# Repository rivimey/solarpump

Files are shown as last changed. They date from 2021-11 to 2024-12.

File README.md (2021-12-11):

Solar powered Water pump controller
===================================

## Introduction

The project has been to put together a water pump powered by a solar panel, with a battery
for reserve power. The need was to pump water from a stream beside allotment garden up to
the allotment for watering plants. The whole unit needs to be completely portable because
the area was was prone to theft.

## Initial version

An initial version was created using off the shelf components, and it worked to a degree.
The solar panel linked to the battery using a cheap solar controller, PWM based, and the
rest of the circuit was wire and switches.

Parts:

 - VerRich Diaphragm pump, 12V Water Pumps 70W Self Priming Pump 6 L/Min

 - Photonic Universe 10A Solar Charge Controller for up to 160W panel.

 - BETOP 60W foldable solar panel kit, 18V.

 - 12V LED Panel Digital Voltmeter Color LED Digital Display
 
 - 12V 20A illuminated rocker switches.

 - 3-pin XLR plugs and sockets for the Solar input

This was constructed with the battery, controller and other wiring inside a wooden box
bought from Amazon, and with the pump screwed to the top (this helps ensure that any
drips of water and electricity don't interact!)

## Second design

A second version was designed with the intention of supporting MPPT conversion and also
to provide additional information about the current flows. This was because placement of
the panel in the prevailing sunlight was easier when you have feedback on what is going
on.

However, this second design was never built -- I was never sure enough it would work to
make it worth getting a PCB built. I had done a lot of reading around the topic of MPPT
converters and was starting to get some idea of the issues and constraints, and could
see that what I had would probably have issues.

I did get as far as a KiCad PCB design, though:

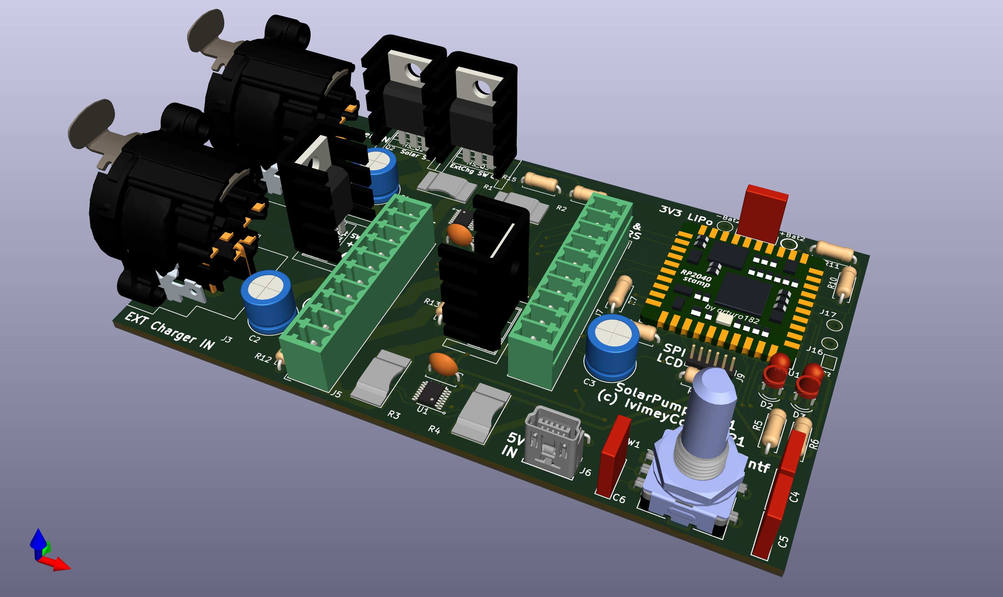
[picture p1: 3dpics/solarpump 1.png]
The abandoned Solarpump v2


## Second build

A new version was built... mostly using the components of the first version in a larger
box (a two bottle "wine presentation" box with a nice looking, and water repellant, red
varnish). This allowed a much better arrangement of the wiring, and made room for a 12V
Car Accessory connector, which was supposed to be helpful for a camping trip.

For this version, a 3D CAD model was built in Blender 3D to verify the dimensions and
fit.

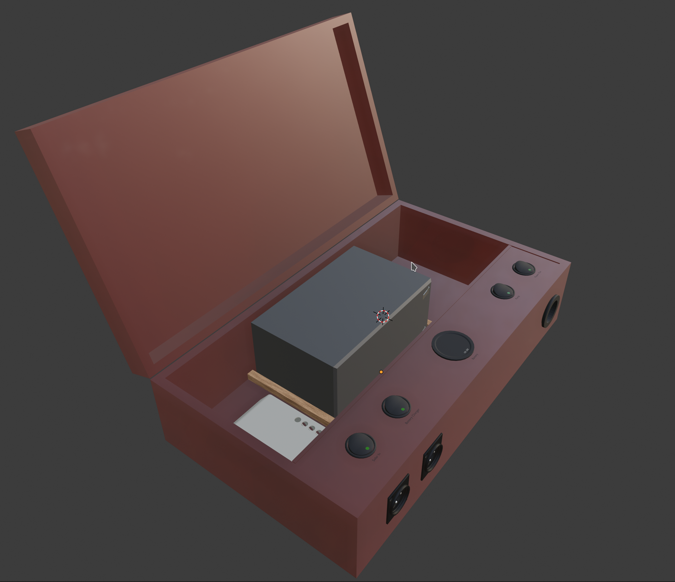
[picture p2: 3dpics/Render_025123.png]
Solar pump in its new box


## Third design

An Intervention came along, in the way of the "DIY 1KW MPPT Solar Charge Converter"
build, published on Instructables. This finally showed a path -- to be fair, not
so very different from my earlier attempt but far better explained and, critically,
tested! I resolved to rebuild my earlier design around this base.

The Instructables build is https://www.instructables.com/DIY-1kW-MPPT-Solar-Charge-Controller/
and there are links to the firmware and design files in that article.

A design goal for this version was to increase the flow rate somewhat, as although the
existing pump worked, it was rather slow. I eventually settled on the Seaflo 41 Series
DC Water System Pump 12V 12.5 LPM, which is up to about 2.5x higher flow rate.

Another design goal is to support measurement of water flow rate, so the unit can
keep track of total water pumped and water pumped per session. While not strictly
necessary this was something I felt was important.

Compared to that version, I decided to:

  - use the Solderparty RP2040 Stamp, partly because I had it and like it;

  - use an alternate half-bridge driver, because the 2104/5 is out of stock at present
    and the new one integrates a diode;

  - use an alternate current sensor (ACS758), because the article was quite critical of
    the one suggested (ACS712). I can't tell from the datasheet if it's an improvement,
    though :-(

  - use more current sensors, to avoid needing to estimate current output from current
    input, partly to monitor more things directly;

  - use 3 separate SM power supply devices for local power, rather than the arrangement
    in the original, which looked clunky;

  - use a different, and 8 channel, ADC to measure the extra circuits, and also enabling
    fast 16-bit sampling and faster MCU comms via SPI. It's slightly more expensive but
    not a lot, and overall better;

The big change I added was one I alluded to in an earlier mail: I essentially have 2
separate buck converters now, rather than just one, because I wanted to:

  - support MPPT input (eg. 18V);

  - support a controllable battery voltage for charging/float purposes (eg. 15V);

  - support a controllable output voltage (sep from battery) to e.g. control DC pump
    speed (eg. 9V to 12.5V).

So I've essentially got:  MPPT => [Battery] => Simple Buck => Output.

This circuit then has two, switchable, outputs, rather than one, which I hope I've
designed right this time! The purpose is to support a fixed link to the pump, plus an
'Aux' circuit for e.g. a car cig socket, for use when e.g. camping. My intention is that
the two outputs are not used at the same time, but the circuit allows that option. I
decided that USB power delivery, while nice, would be via a commercial car adapter,
not built in.

I have derated the components slightly compared to the original, supporting only up
to 48V input and up to about current output 18A rather than the 80V and 30A original,
as this is meant to be a portable unit and not destined for huge batteries or panel
arrays. On the battery front I'm intending to change from a 12V lead acid battery to
a 4S3P Lithium one based on twelve 18650 batteries + controller for a 14V output. It
should help reduce the weight (the new pump, now 3 gal/min rather than 1gal/min of
earlier, is heavier!).

The second smaller board is for a 'front panel', which I envisage with a large
"emergency stop" pushbutton, a digital rotary encoder, and a Pimoroni "Pico Display
Hat", which is a small LCD on a 40pin R-Pi Pico footprint with 4 small pushbuttons and
an RGB led. Most of that is interfaced via an MCP 16-pin IO adapter on the I2C bus,
except for the SPI bus for the display itself.

Not shown in the circuit because it's off-board, the main on/off switch will be an
SPST switch between the battery and the PCB.

Some pictures of the build so far (from KiCad):

PCB for Solarpump v3

PCB for Solarpump v3

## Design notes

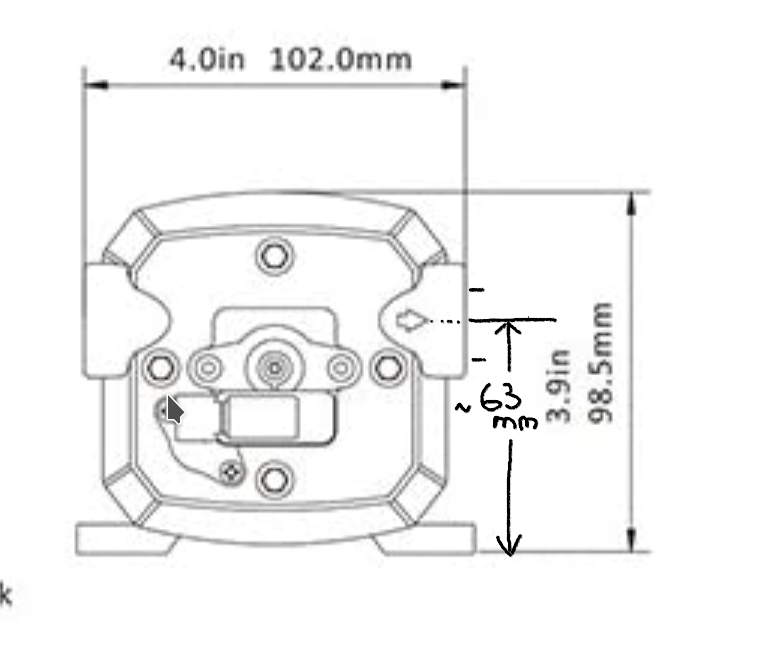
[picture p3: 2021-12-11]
Docs/Pump_outline.png

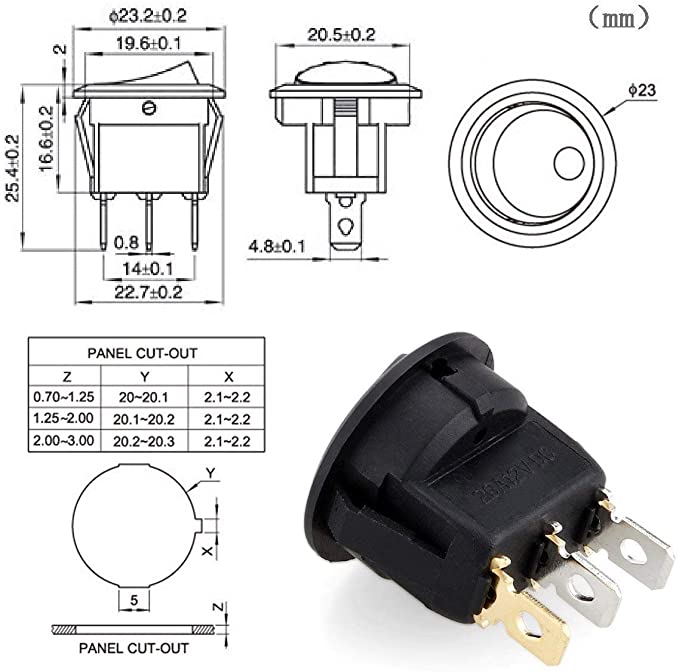
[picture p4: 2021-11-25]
Docs/Toggle_SW_618fWi4n+FL.AC_SX679.jpg

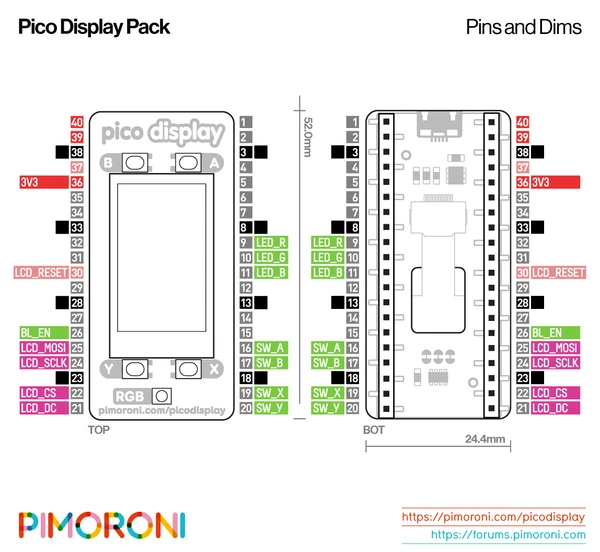
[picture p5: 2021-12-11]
Docs/displaypack_600x600.png

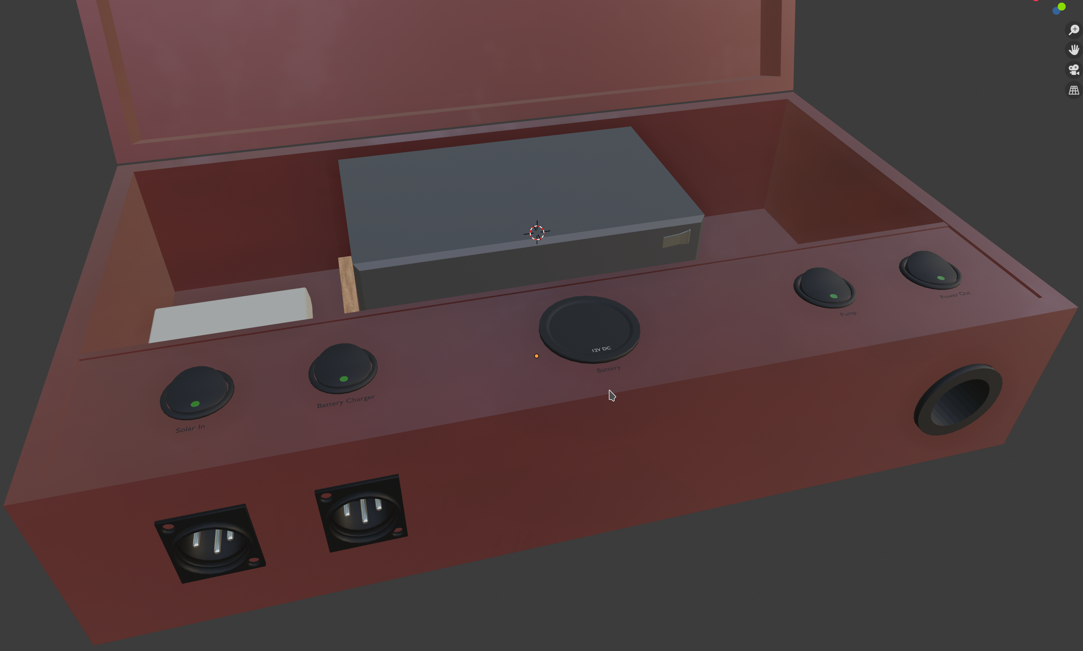
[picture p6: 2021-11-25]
3dpics/Render_025204.png

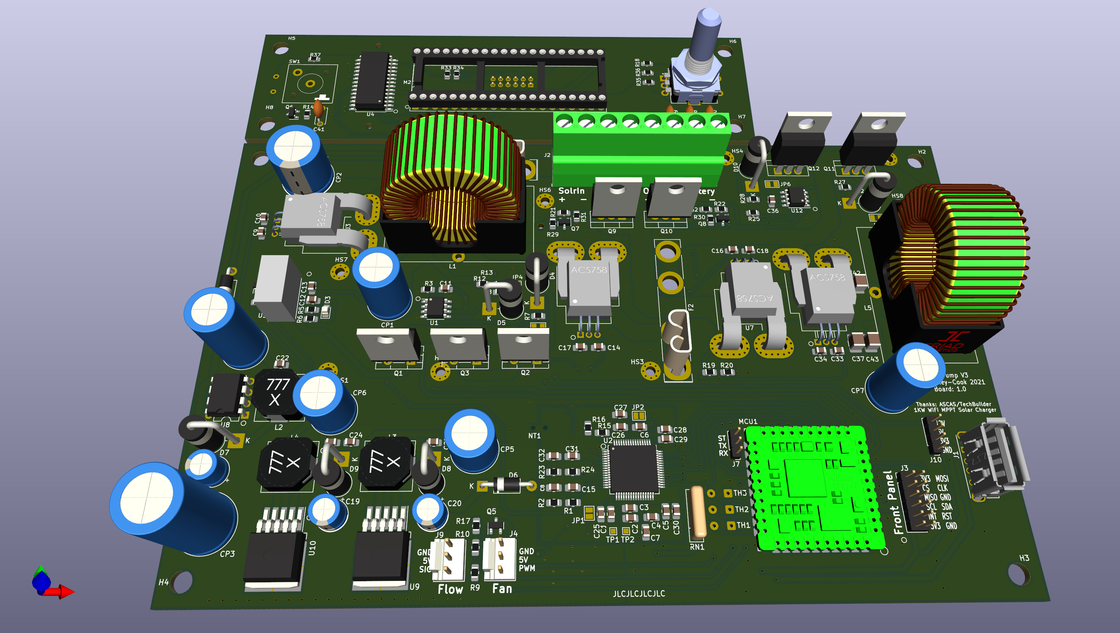
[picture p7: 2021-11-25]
3dpics/solarpumpv3_2.png

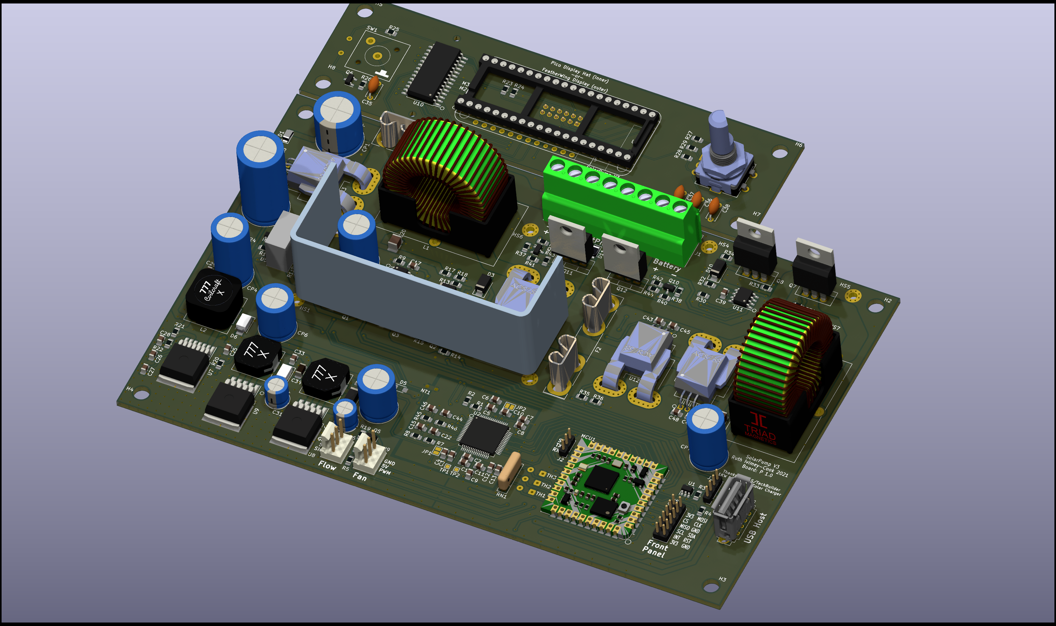
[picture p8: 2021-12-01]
3dpics/solarpump3_11r.png

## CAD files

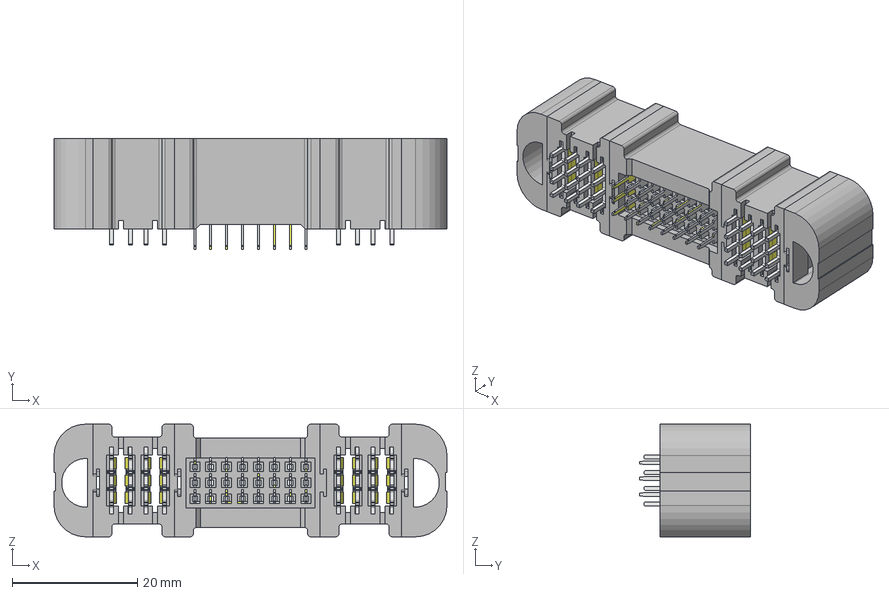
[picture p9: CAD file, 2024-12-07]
3dmodels/ET60S-D02-3-08-D02-X-V1-S.step
62.8 x 17.7 x 18.0 mm
ET60S-24-V1_signal_terminal
ET60S-D02-V1_power_terminal x 2
ET60S-V1_guide_post_left
ET60S-D02-V1_power_pins x 2
ET60S-D02-V12_power_pins x 2
ET60S-V1_guide_post_right
ET60S-24-V1_signal_pins
ET60S-24-V12_signal_pins

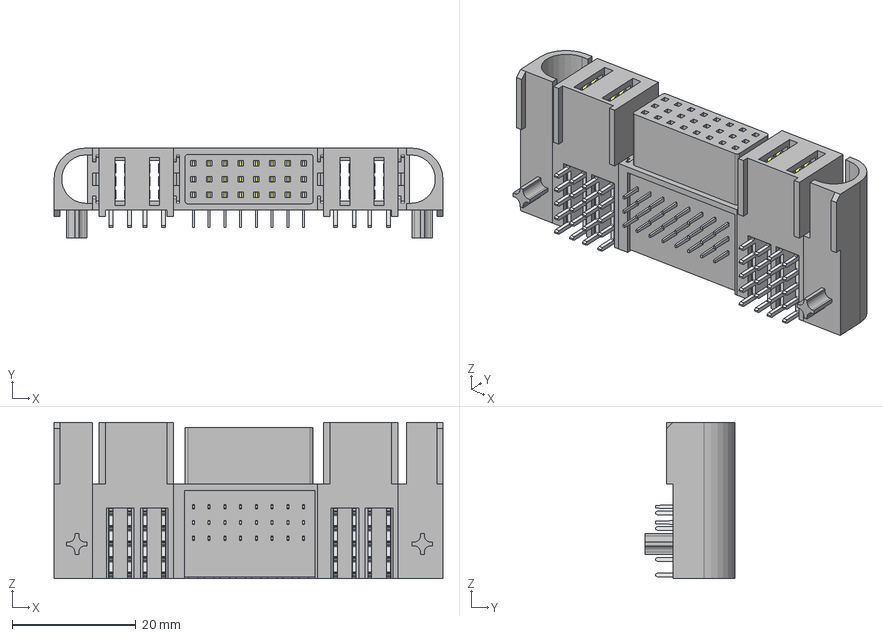
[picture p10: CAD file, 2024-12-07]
3dmodels/ET60S-D02-3-08-D02-L-R1-S.stp
62.8 x 14.5 x 25.2 mm
ET60S-24-R1_signal_terminal
ET60S-D02-R1_power_terminal x 2
ET60S-R1_guide_post_left
ET60S-D02-R1_power_pins x 2
ET60S-D02-R12_power_pins x 2
ET60S-R1_guide_post_right
ET60S-24-R1_signal_pins
ET60S-24-R12_signal_pins

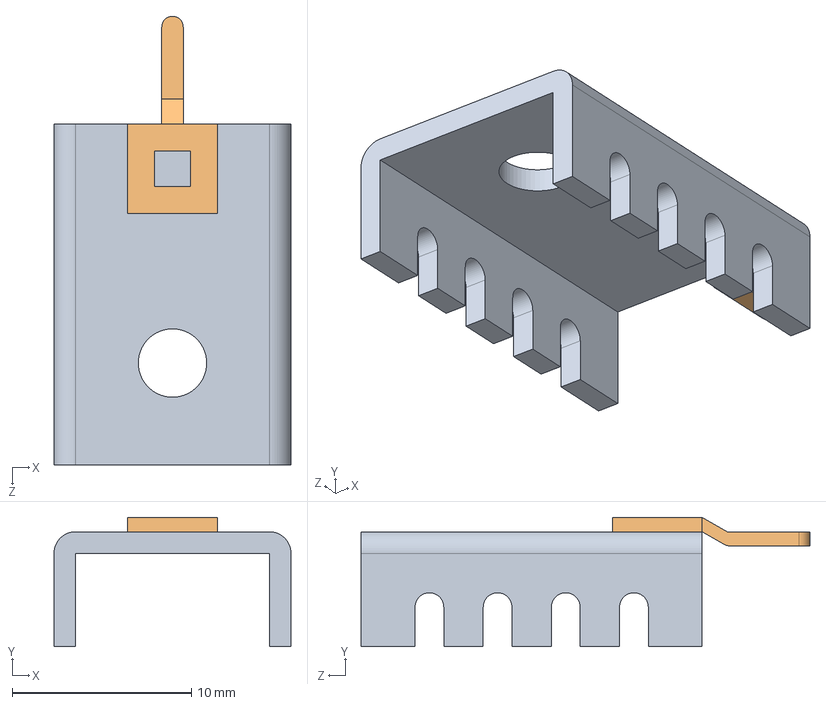
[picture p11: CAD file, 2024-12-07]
3dmodels/User Library-D01PA.STEP
13.2 x 7.20 x 25.0 mm

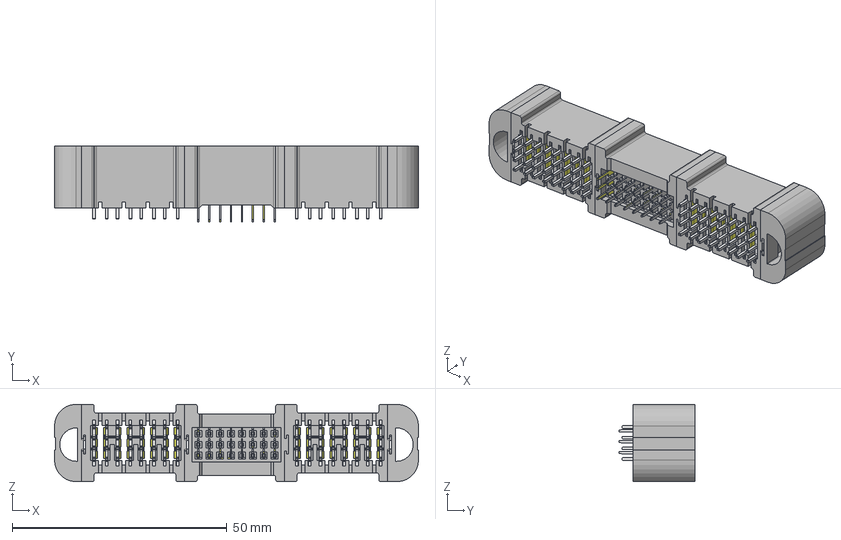
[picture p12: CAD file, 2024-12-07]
3dmodels/ET60S-D04-3-08-D04-X-V1-S.step
84.8 x 17.7 x 18.0 mm
ET60S-24-V1_signal_terminal
ET60S-D04-V1_power_terminal x 2
ET60S-V1_guide_post_left
ET60S-D04-V1_power_pins x 2
ET60S-D04-V12_power_pins x 2
ET60S-V1_guide_post_right
ET60S-24-V1_signal_pins
ET60S-24-V12_signal_pins

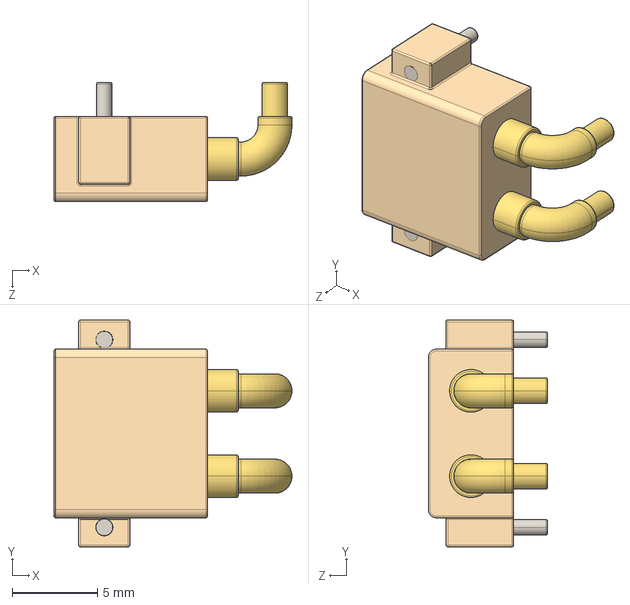
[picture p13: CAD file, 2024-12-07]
3dmodels/AMASS-XT30PW-M.STEP
13.9 x 13.3 x 7.00 mm

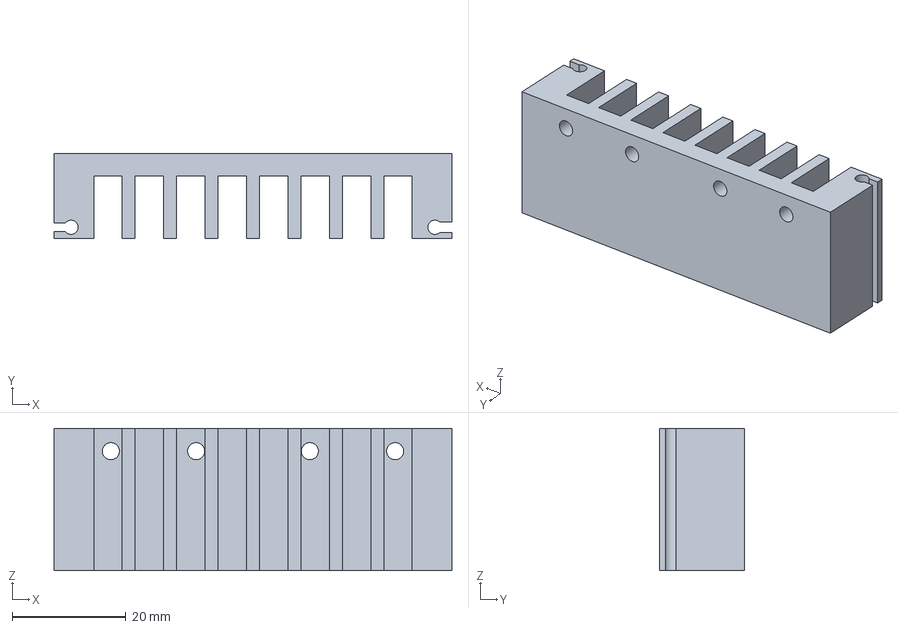
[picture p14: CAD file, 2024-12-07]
3dmodels/RADIATEUR_4_TROUS.step
70.0 x 15.0 x 25.0 mm

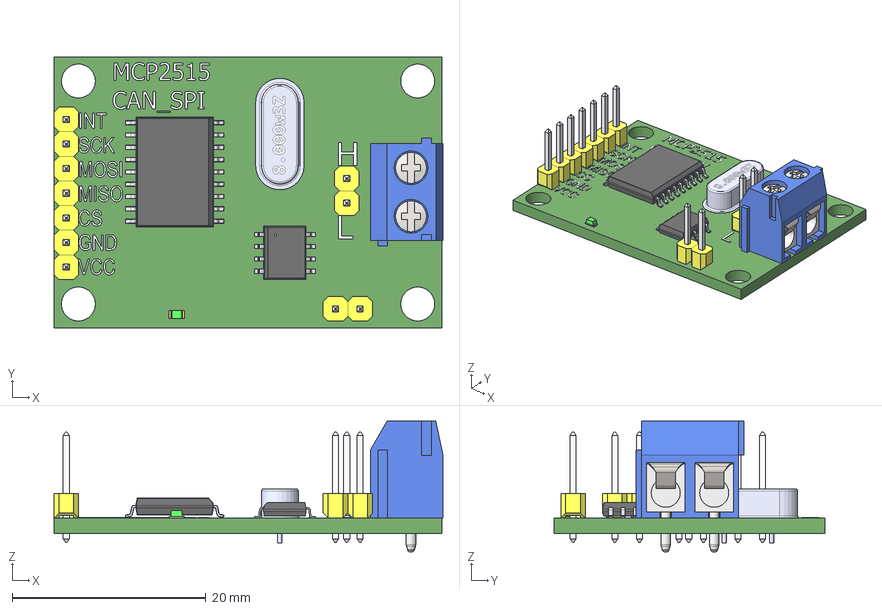
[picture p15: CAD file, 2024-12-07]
3dmodels/MCP2515 CAN_SPI.step
40.1 x 28.0 x 13.5 mm
so_ic_wide_18pin
PCB CAN SPI
so_ic_8pin
led_green_0603
ABRACON_ABL-8.000MHZ-B2
Pin Header 7 x 1 TH 2.54mm Pitch
Pin Header 2 x1 TH 2.54mm Pitch x 2
TE_1776244-2

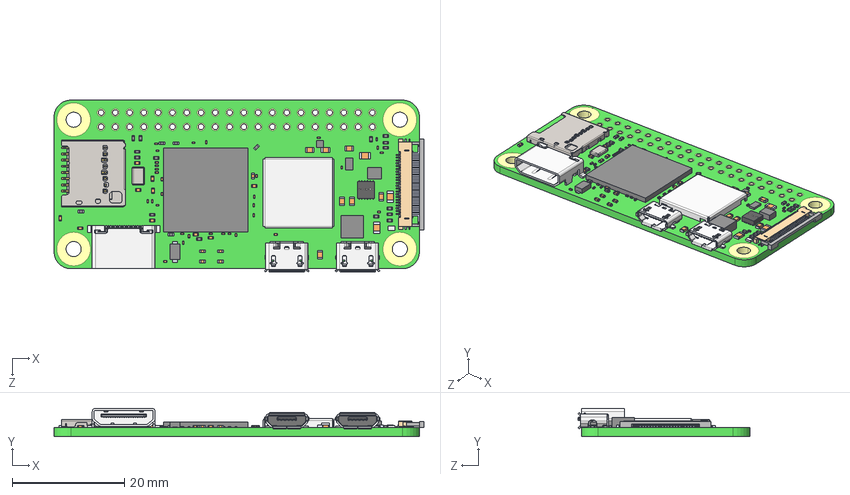
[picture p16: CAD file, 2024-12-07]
3dmodels/Raspberry Pi Zero 2 W.STEP
65.8 x 5.05 x 30.6 mm
PCB, Raspberry Pi Zero 2 W
RP3A0-AU 2105 201221C, Raspberry Pi Zero 2 W
MicroUSB Port, Raspberry Pi Zero 2 W x 2
SD Card Slot, Raspberry Pi Zero 2 W
Wireless Module Cover, Raspberry Pi Zero 2 W
Crystal Resonator, Raspberry Pi Zero 2 W
LED, Raspberry Pi Zero 2 W
Diode, Schottky, Raspberry Pi Zero 2 W
54548-2271, 22 Pin FPC Connector, Raspberry Pi Zero 2 W
Mini HDMI Receptacle Port, Raspberry Pi Zero 2 W
PAM2306AYPKE, Switching Voltage Regulators Dual PWM Step-Down 40uA 1A 1.5MHz, Raspberry Pi Zero 2 W
RT9081A-1BGQZA, Fixed LDO Voltage Regulator, 0.8V-5.5Vin, 140mV drop, 1.25Vout, 0.5Aout, Raspberry Pi Zero 2 W_default
RT8088AWSC, IC Reg Buck Prog 3A Sync 15WLCSP, Raspberry Pi Zero 2 W_default
SMD Inductor, Configurable, Raspberry Pi Zero 2 W_L1
SMD Inductor, Configurable, Raspberry Pi Zero 2 W_L2
SMD Capacitor, Configurable, Raspberry Pi Zero 2 W_C1 x 3
SMD Capacitor, Configurable, Raspberry Pi Zero 2 W_C3 x 7
SMD Capacitor, Configurable, Raspberry Pi Zero 2 W_C2 x 31
SMD Capacitor, Configurable, Raspberry Pi Zero 2 W_C10 x 15
SMD Resistor, Configurable, Raspberry Pi Zero 2 W_R1 x 20
SMD Resistor, Configurable, Raspberry Pi Zero 2 W_R12

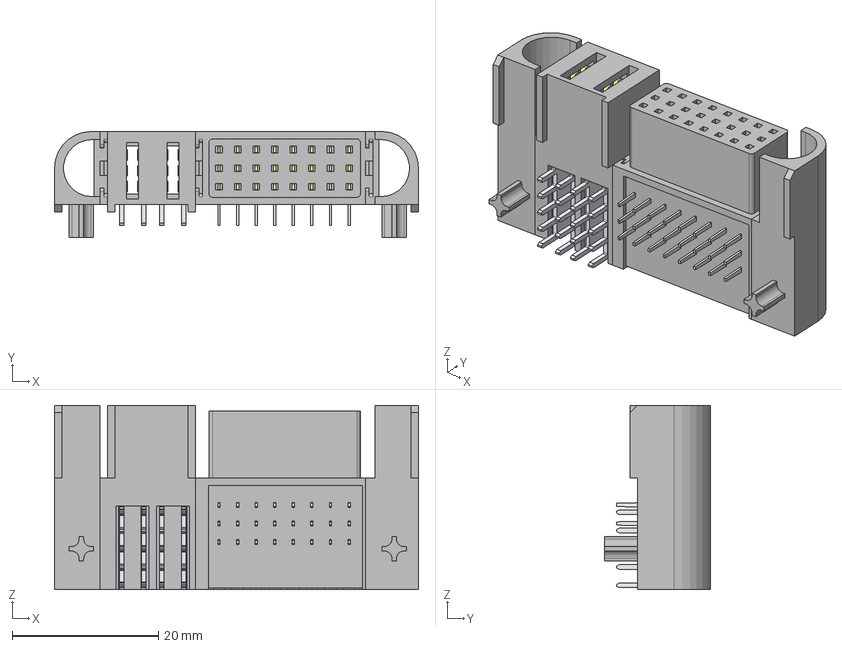
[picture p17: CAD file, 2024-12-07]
3dmodels/ET60S-000-3-08-D02-L-R1-S.step
49.8 x 14.5 x 25.2 mm
ET60S-24-R1_signal_terminal
ET60S-D02-R1_power_terminal
ET60S-R1_guide_post_left
ET60S-D02-R1_power_pins
ET60S-D02-R12_power_pins
ET60S-000-R1_power_terminal
ET60S-R1_guide_post_right
ET60S-000-R1_power_pins
ET60S-000-R12_power_pins
ET60S-24-R1_signal_pins
ET60S-24-R12_signal_pins

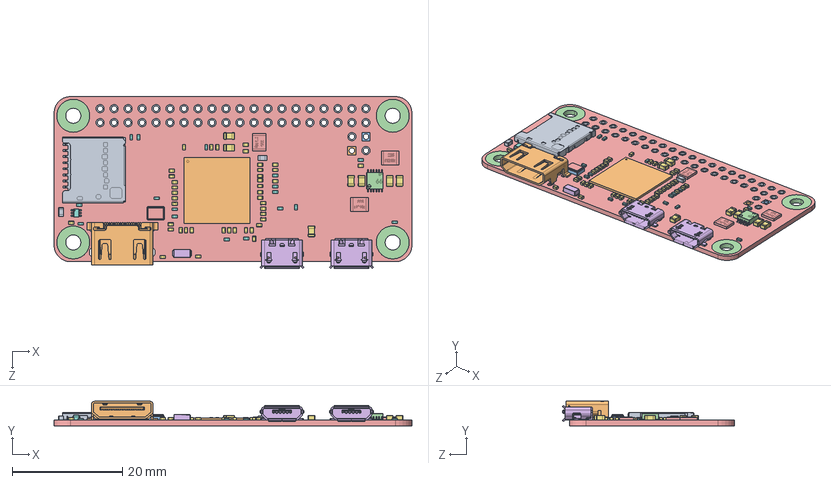
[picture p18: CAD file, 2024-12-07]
3dmodels/RapberryPiZero.STEP
65.0 x 4.45 x 31.2 mm
Raspberry_pizero_PCB
Micro USB_input_female (short)-SMT x 2
0204 - Capacitor x 34
0204- Resistor x 17
CAP-0306 x 2
Raspberry_pizero_BCM2835 with VC4
Crystal 3.4x2.4mm
32,768 Khz Crystal
0805- Capacitor x 7
0204 - Capacitor Brown x 8
6-Pin SOT
micro sd molex
hdmi type C
Voltage Regulator 3x3mm 12-Pin
1210 inductor x 3

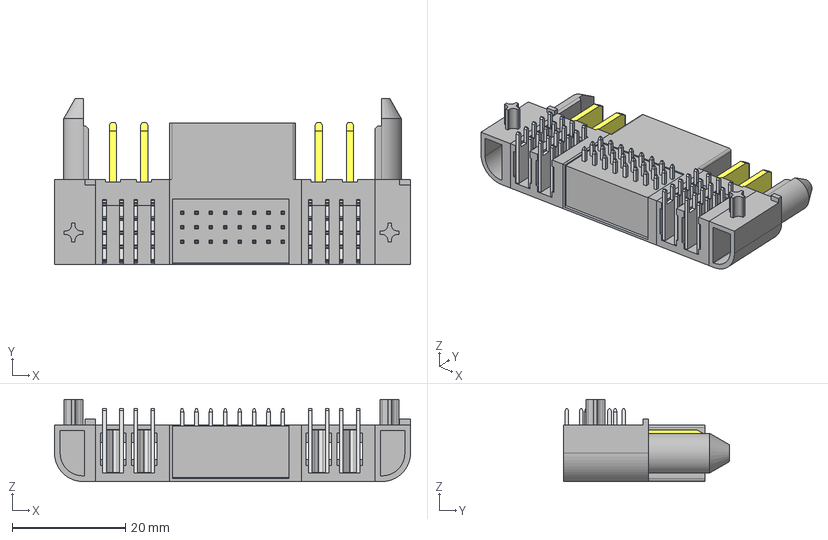
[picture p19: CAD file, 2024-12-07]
3dmodels/ET60T-D02-3-08-D02-X-R1-S.step
62.8 x 29.2 x 14.5 mm
ET60T-24-RT1-GP_st
ET60T-D-02-0_pt x 2
ET60T-RT1-GP_gpl
ET60T-D-02-R1-_ppins_l
ET60T-D-02-R1-2_ppins_l
ET60T-RT1-GP_gpr
ET60T-D-02-R1-_ppr
ET60T-D-02-R1-2_ppr
ET60T-24-R1-_sp
ET60T-24-R1-2_sp

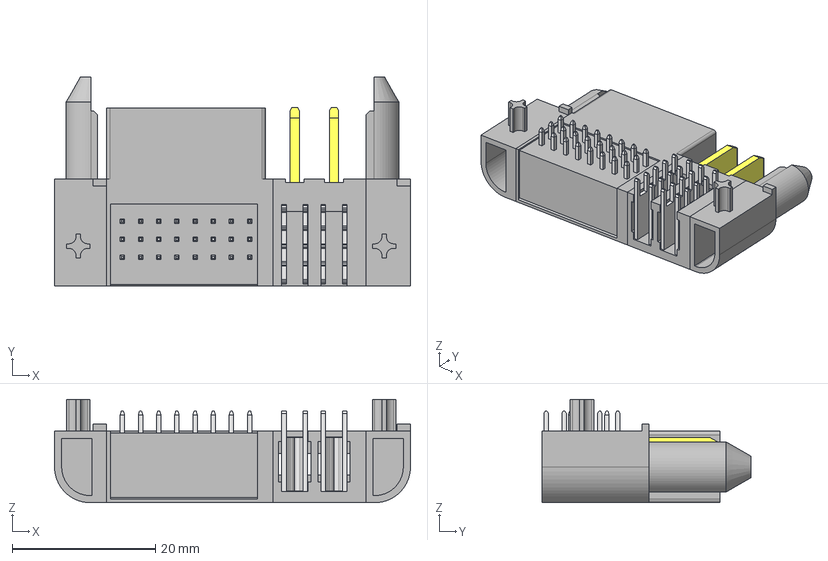
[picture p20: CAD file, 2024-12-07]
3dmodels/ET60T-000-3-08-D02-L-R1-S.stp
49.8 x 29.2 x 14.5 mm
ET60T-24-RT1-GP_st
ET60T-0-00-0_pt
ET60T-RT1-GP_gpl
ET60T-0-00-R1-_ppins_l
ET60T-0-00-R1-2_ppins_l
ET60T-D-02-0_pt
ET60T-RT1-GP_gpr
ET60T-D-02-R1-_ppr
ET60T-D-02-R1-2_ppr
ET60T-24-R1-_sp
ET60T-24-R1-2_sp

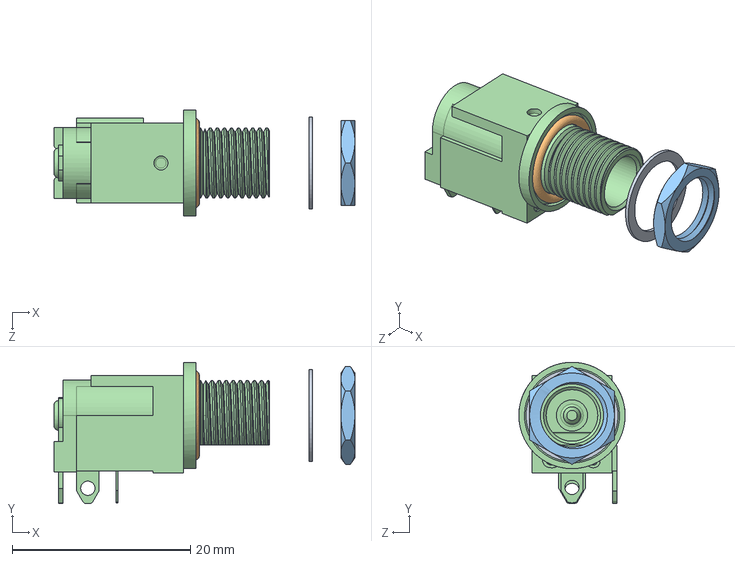
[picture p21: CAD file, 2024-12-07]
3dmodels/RAPC10S.step
33.8 x 15.9 x 11.9 mm

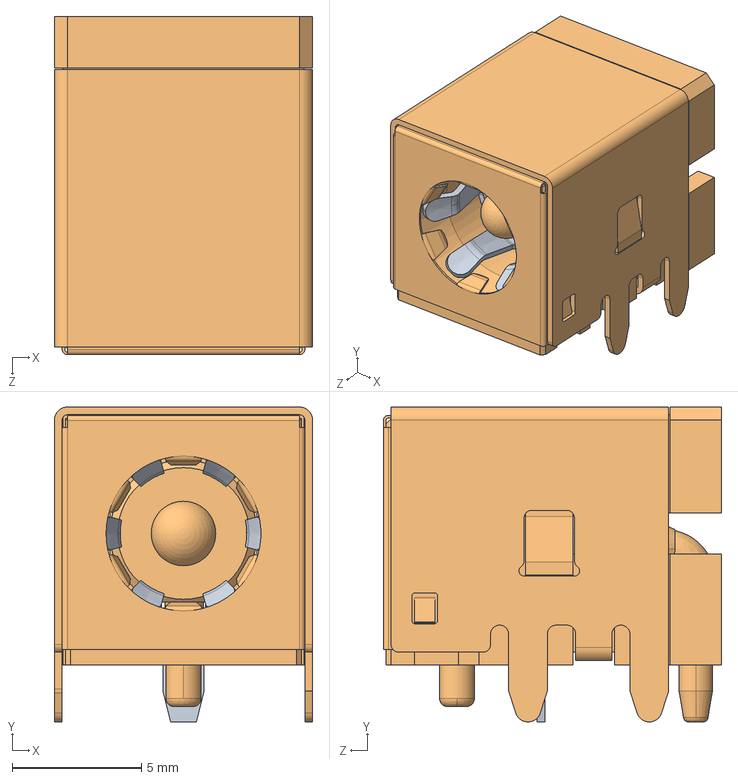
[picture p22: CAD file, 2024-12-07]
3dmodels/Same_Sky_PJ-082BH.step
10.0 x 12.2 x 13.1 mm

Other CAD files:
3dmodels/ET60S-D04-3-08-D04-L-V1-S.stp
3dmodels/ET60T-D02-3-08-D02-L-R1-S.stp
3dmodels/ET60T-000-3-08-D02-X-R1-S.step
3dmodels/ET60T-D02-3-08-000-L-R1-S.stp
3dmodels/1050570001.step
3dmodels/1241.1082.3.step
3dmodels/1241.1082.8.STEP
3dmodels/1241.step
3dmodels/3-d-nc3faah2.step
3dmodels/387006308.step
3dmodels/54-00023.step
3dmodels/Coilcraft-MSS1278H.STEP
3dmodels/DO-214AC.STEP
3dmodels/DO-219AB.stp
3dmodels/ET60S-D02-3-08-D02-L-V1-S.stp
3dmodels/ET60T-D02-3-08-000-X-R1-S.step
3dmodels/Heatsink1-1.step
3dmodels/Heatsink1.step
3dmodels/Heatsink2.step
3dmodels/Led RGB 5mm.STEP
3dmodels/MCP2515 CAN_SPI.stp
3dmodels/OLED_SOG320132A_M383.step
3dmodels/REF-182683-02.step
3dmodels/REF-182684-02.step
3dmodels/RP2040_Stamp.step
3dmodels/USB1040-GF-L-B.step
3dmodels/acs758-1.step
3dmodels/battery12v7ah step.step
3dmodels/coilcraft-mss1038.step
3dmodels/css2h-3920.step
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

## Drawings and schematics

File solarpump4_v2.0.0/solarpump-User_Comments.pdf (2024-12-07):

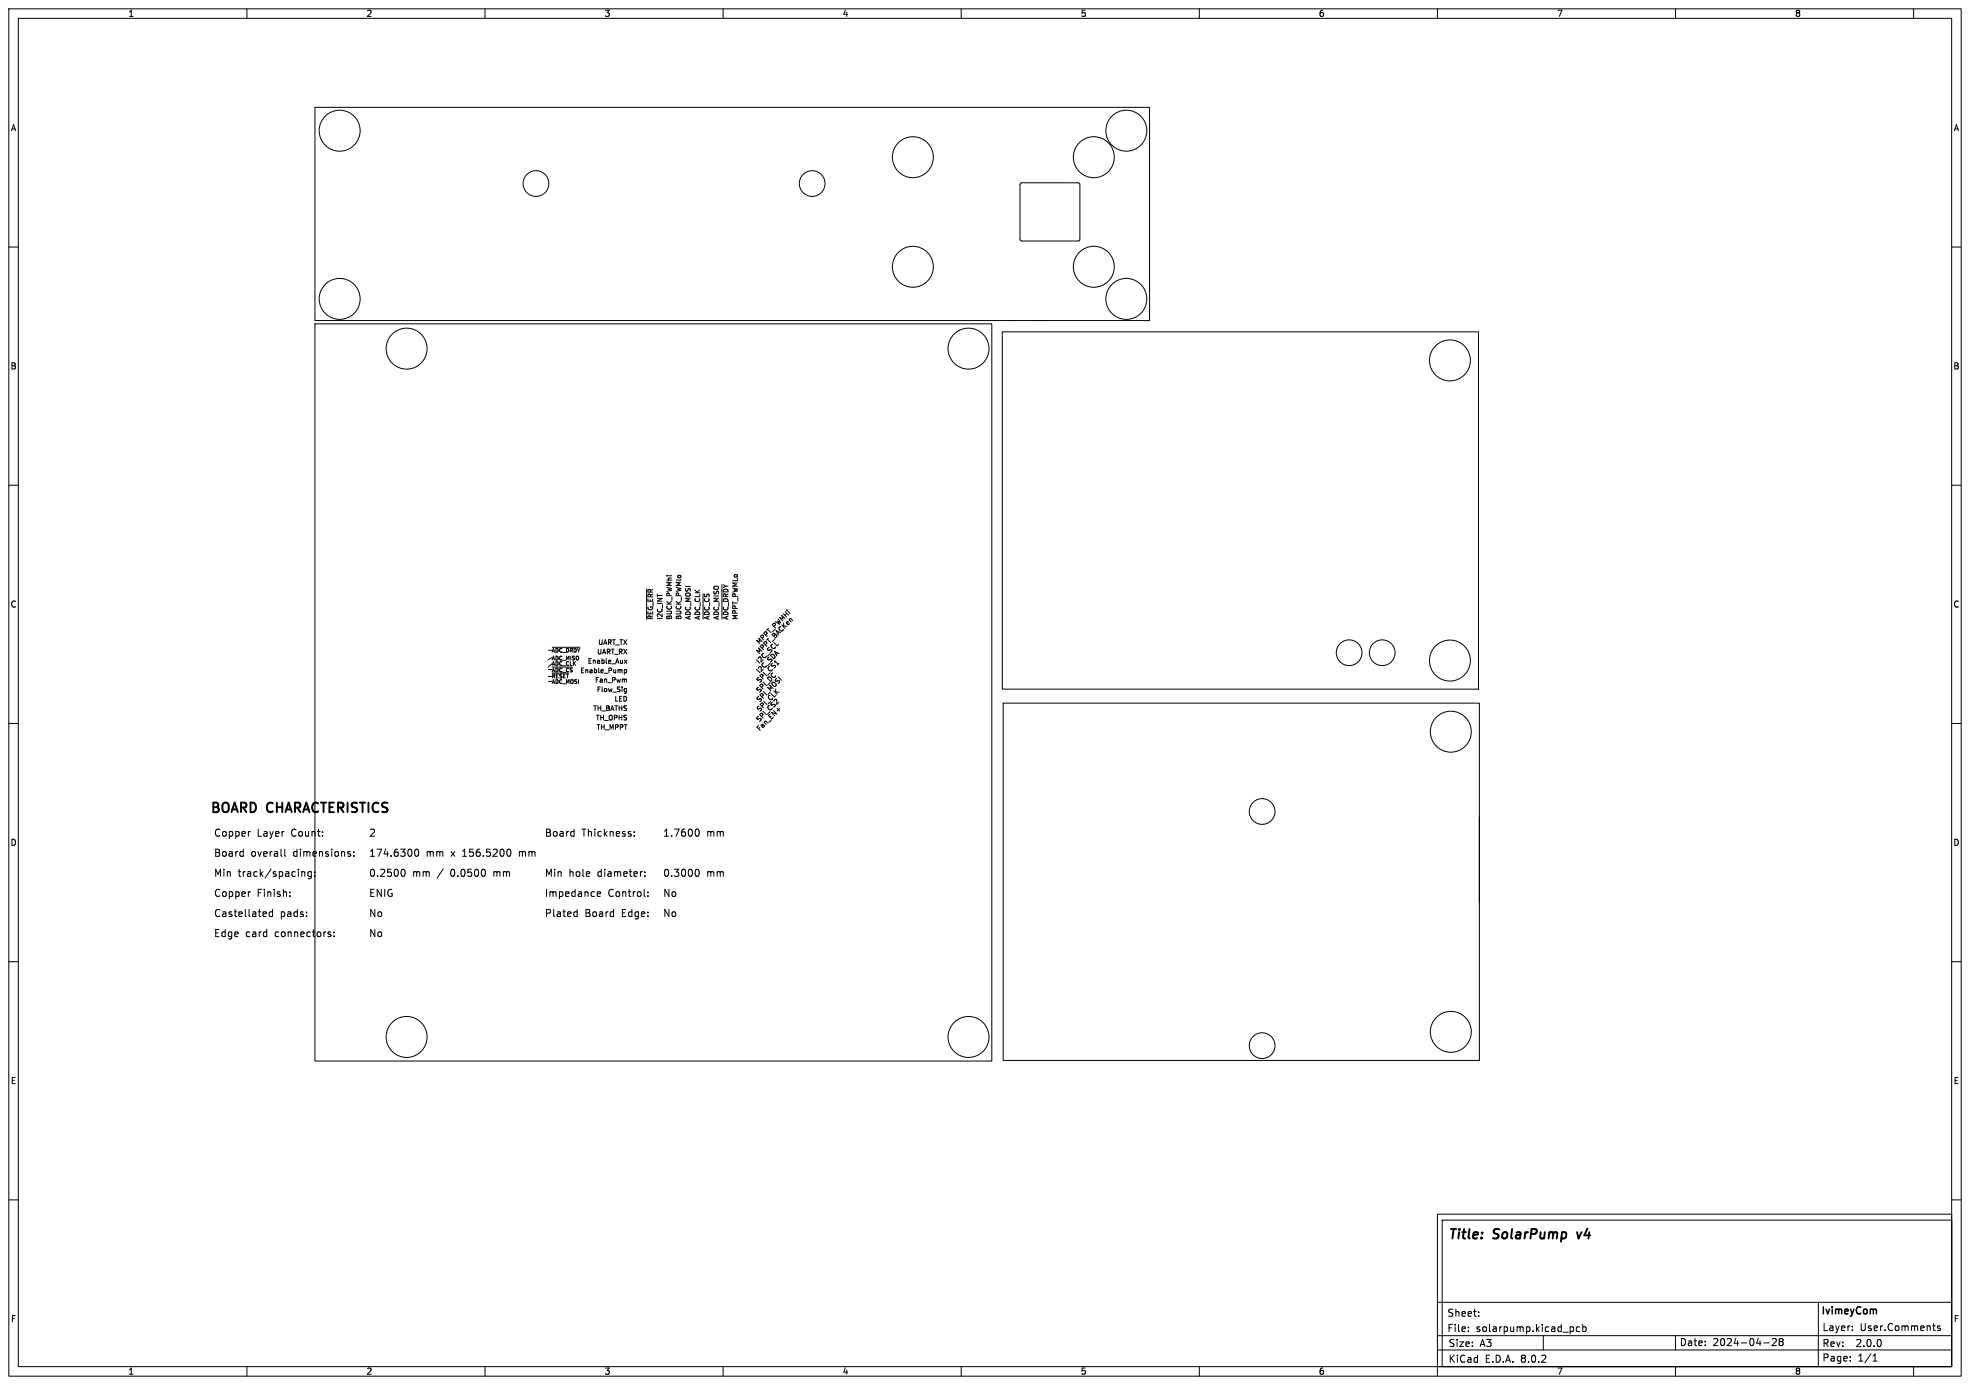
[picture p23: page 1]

SPI_CS1 I2C_SDA ADC_MISO Castellated pads: 174.6300 mm x 156.5200 mm

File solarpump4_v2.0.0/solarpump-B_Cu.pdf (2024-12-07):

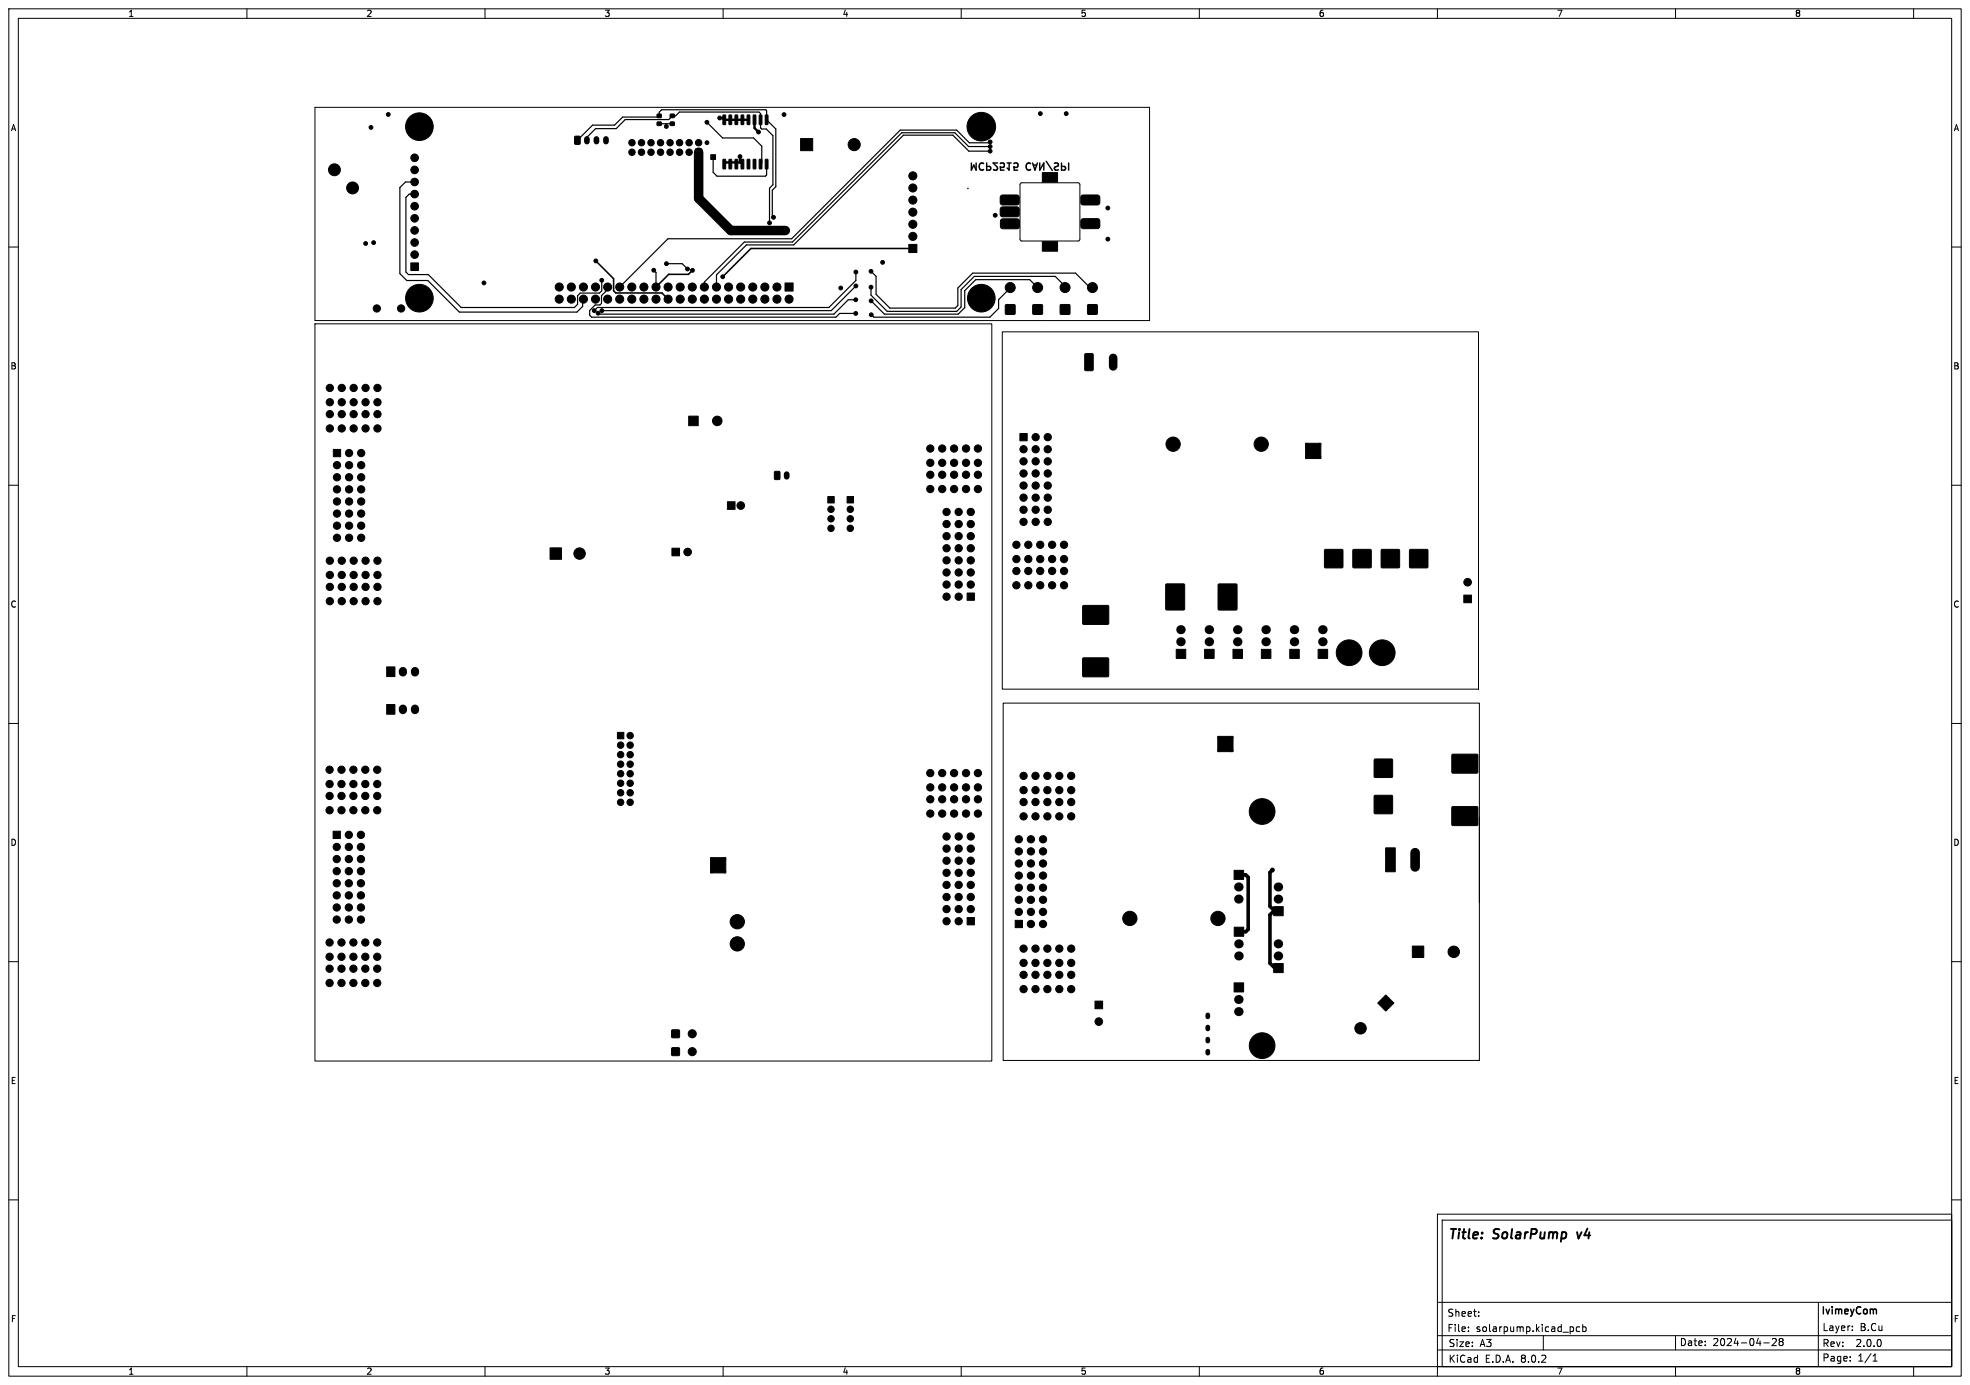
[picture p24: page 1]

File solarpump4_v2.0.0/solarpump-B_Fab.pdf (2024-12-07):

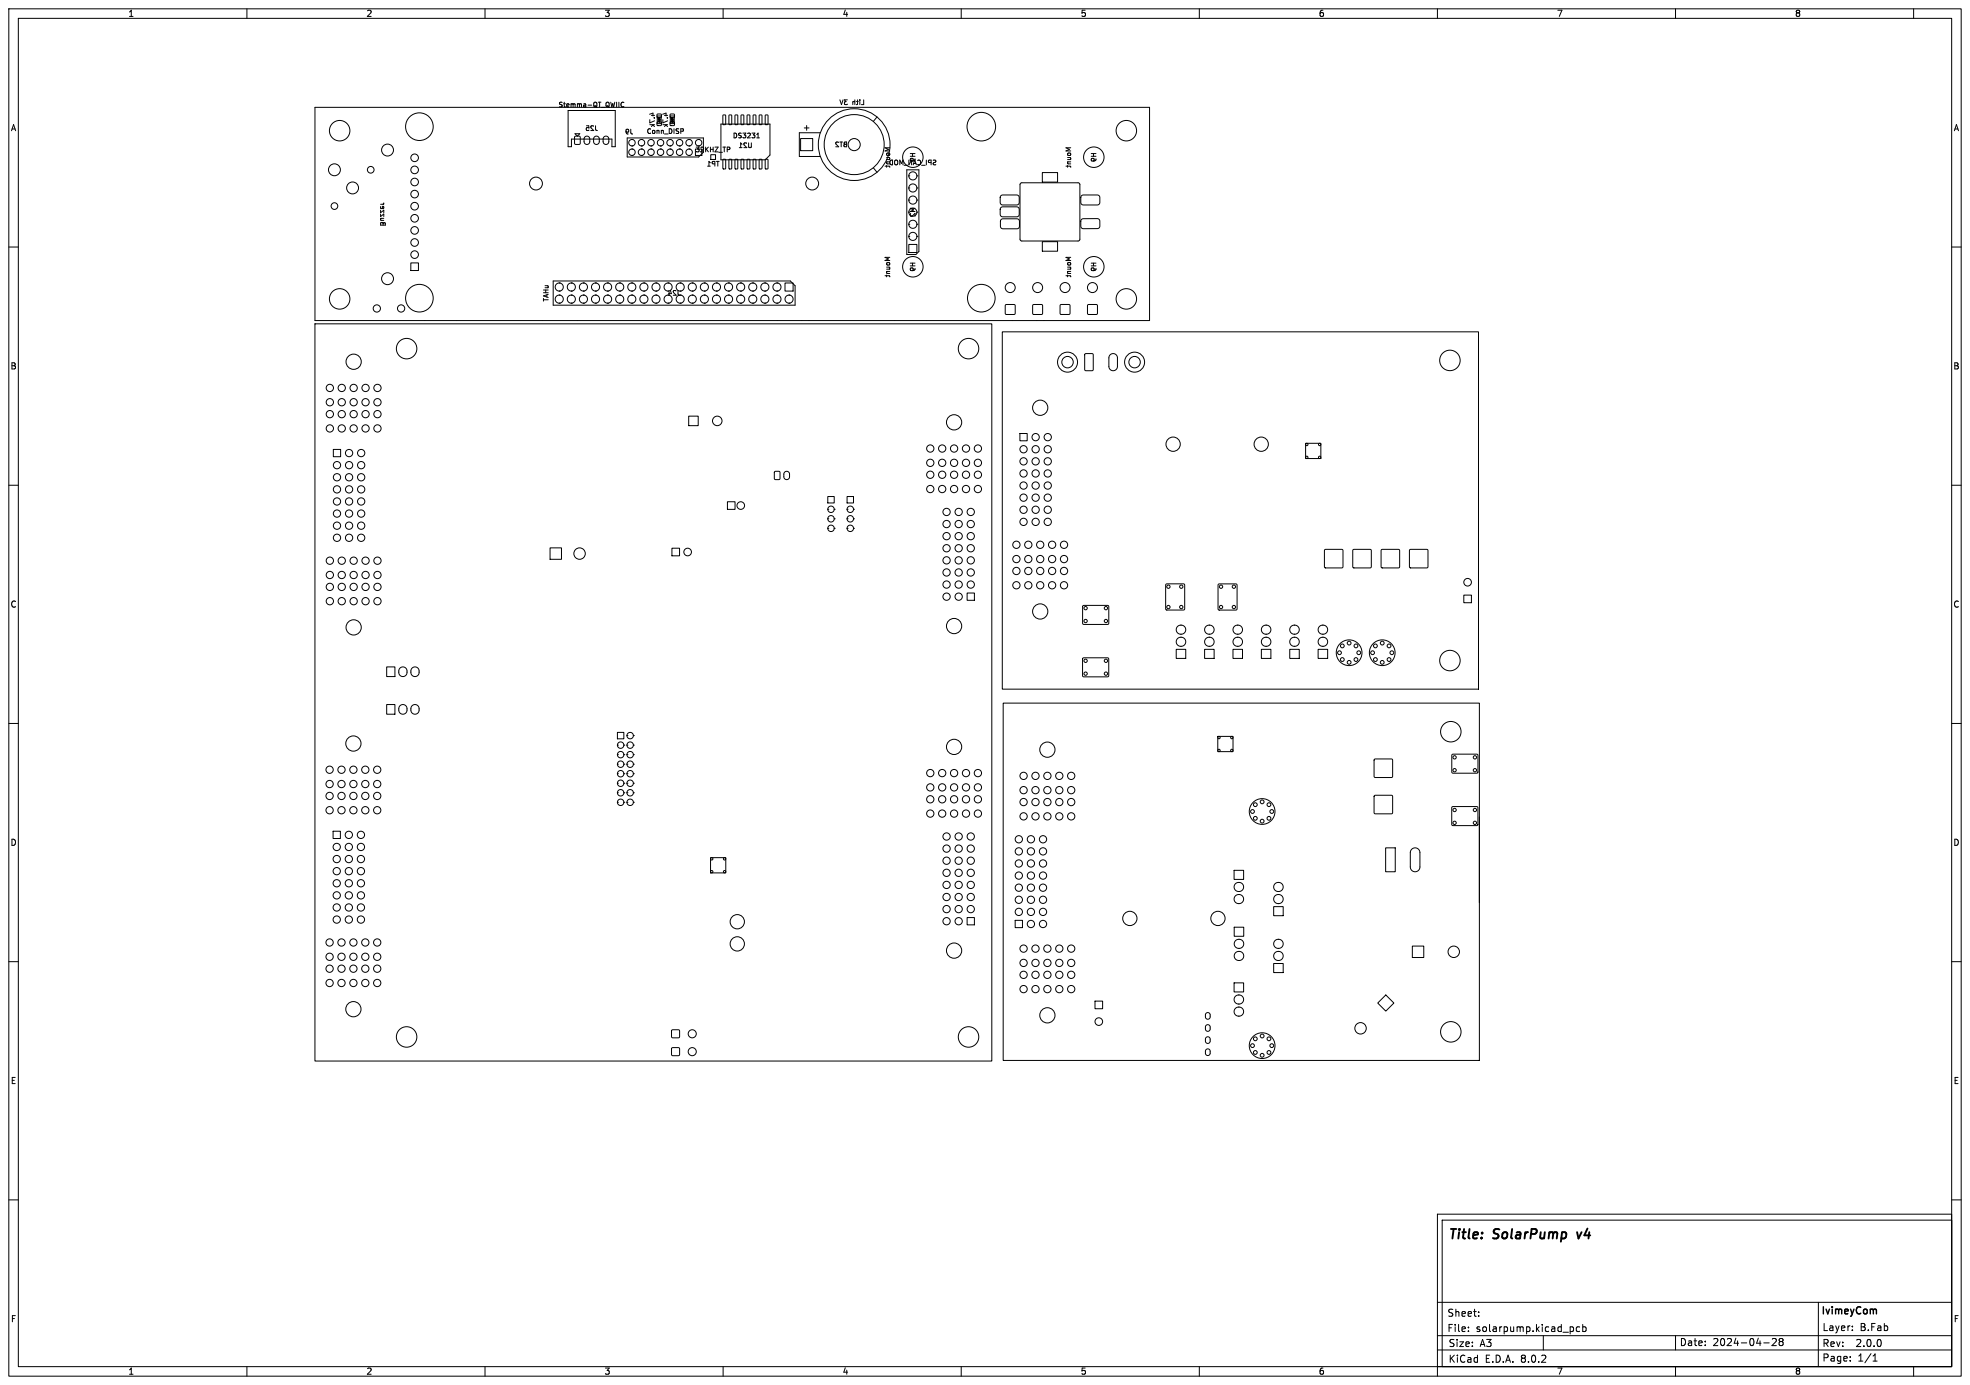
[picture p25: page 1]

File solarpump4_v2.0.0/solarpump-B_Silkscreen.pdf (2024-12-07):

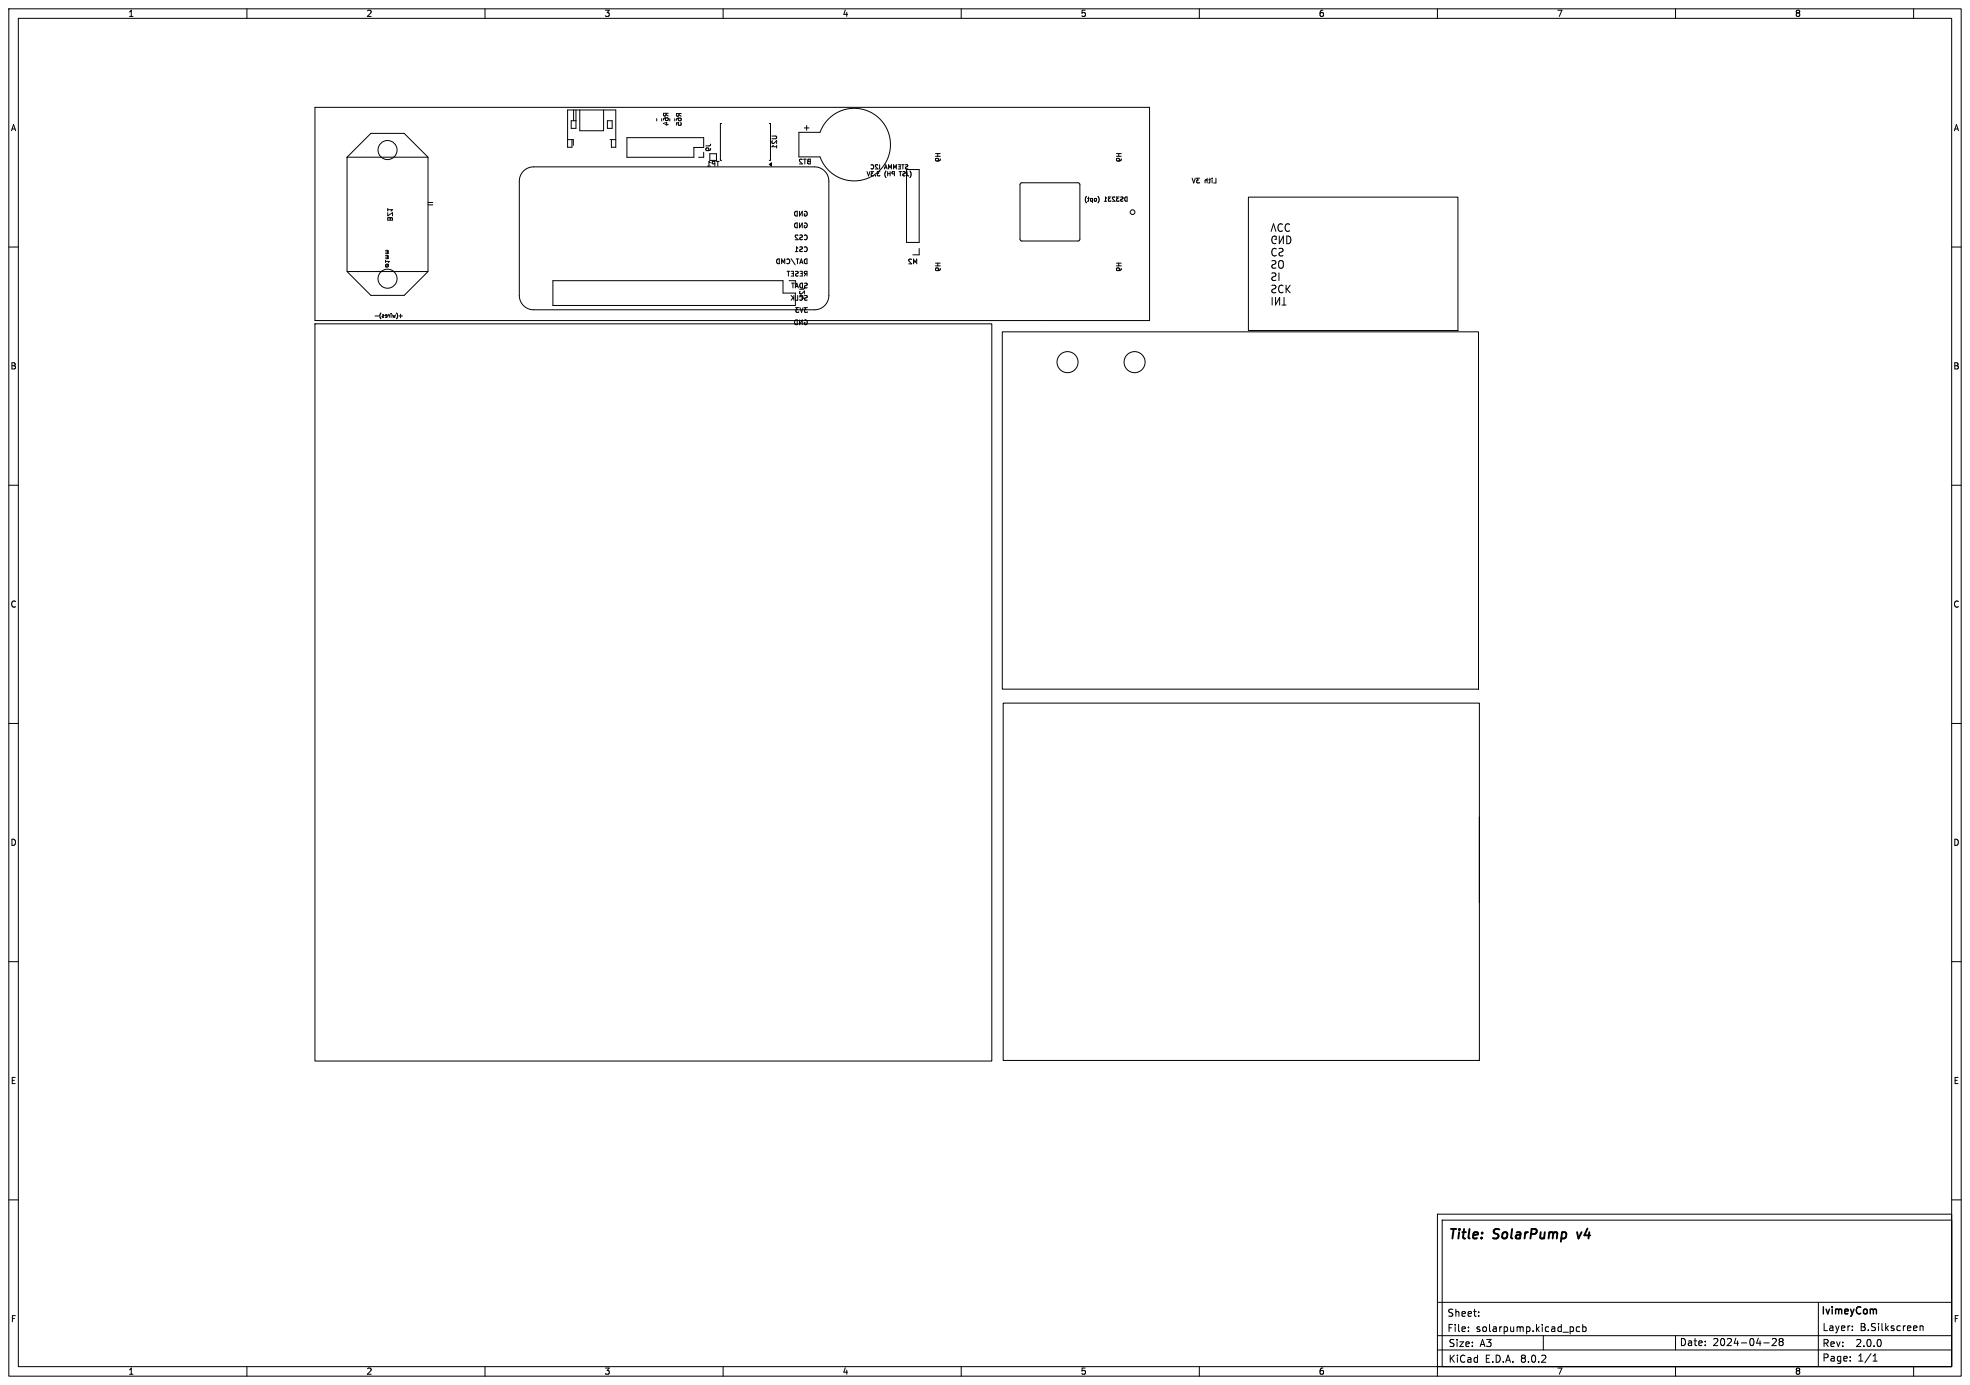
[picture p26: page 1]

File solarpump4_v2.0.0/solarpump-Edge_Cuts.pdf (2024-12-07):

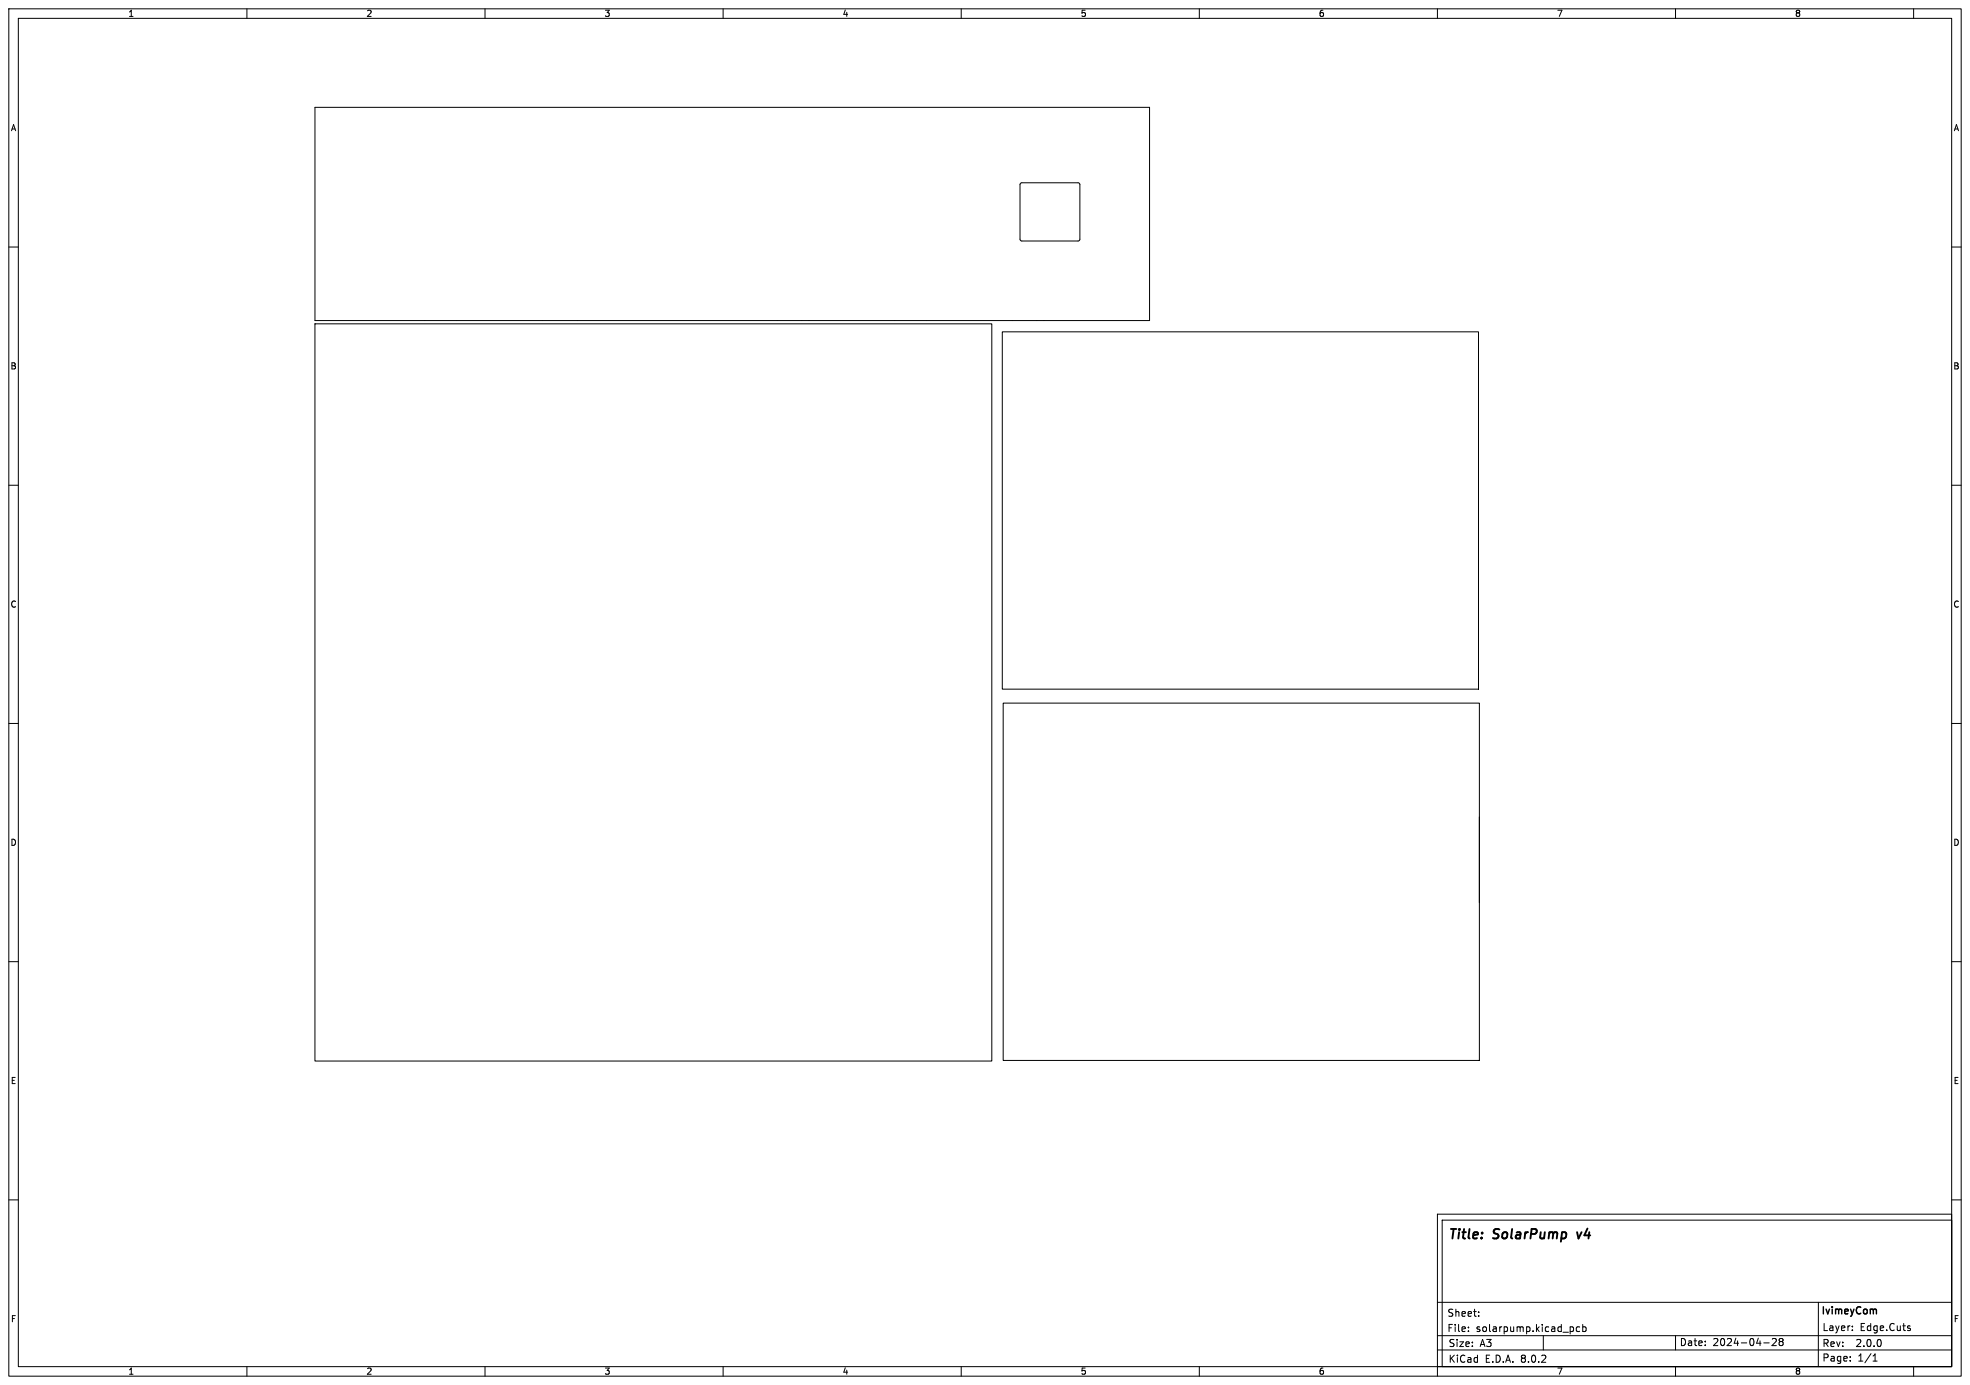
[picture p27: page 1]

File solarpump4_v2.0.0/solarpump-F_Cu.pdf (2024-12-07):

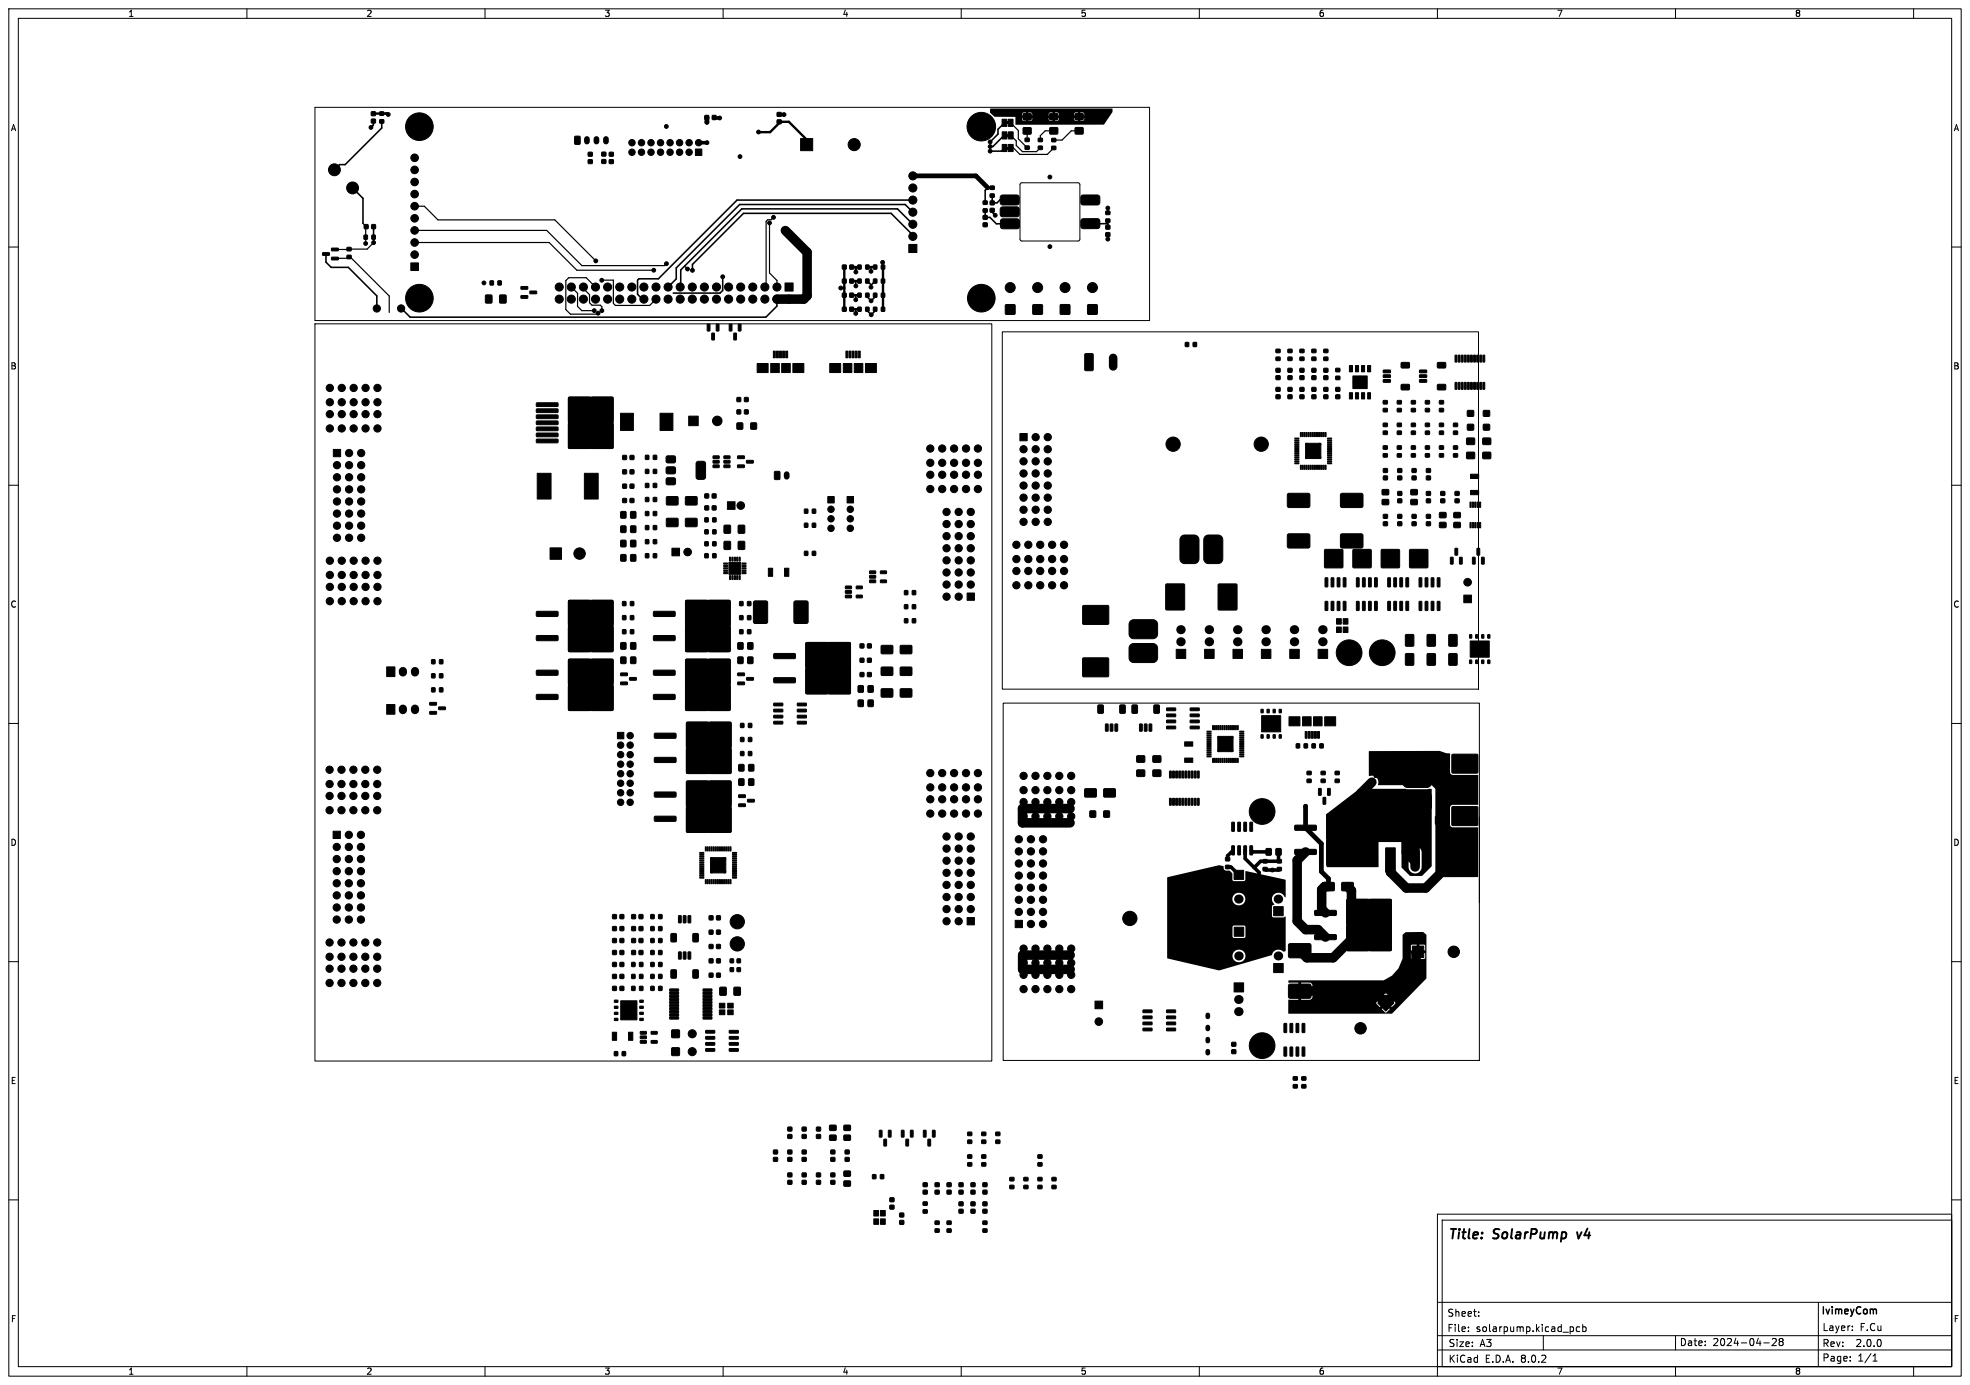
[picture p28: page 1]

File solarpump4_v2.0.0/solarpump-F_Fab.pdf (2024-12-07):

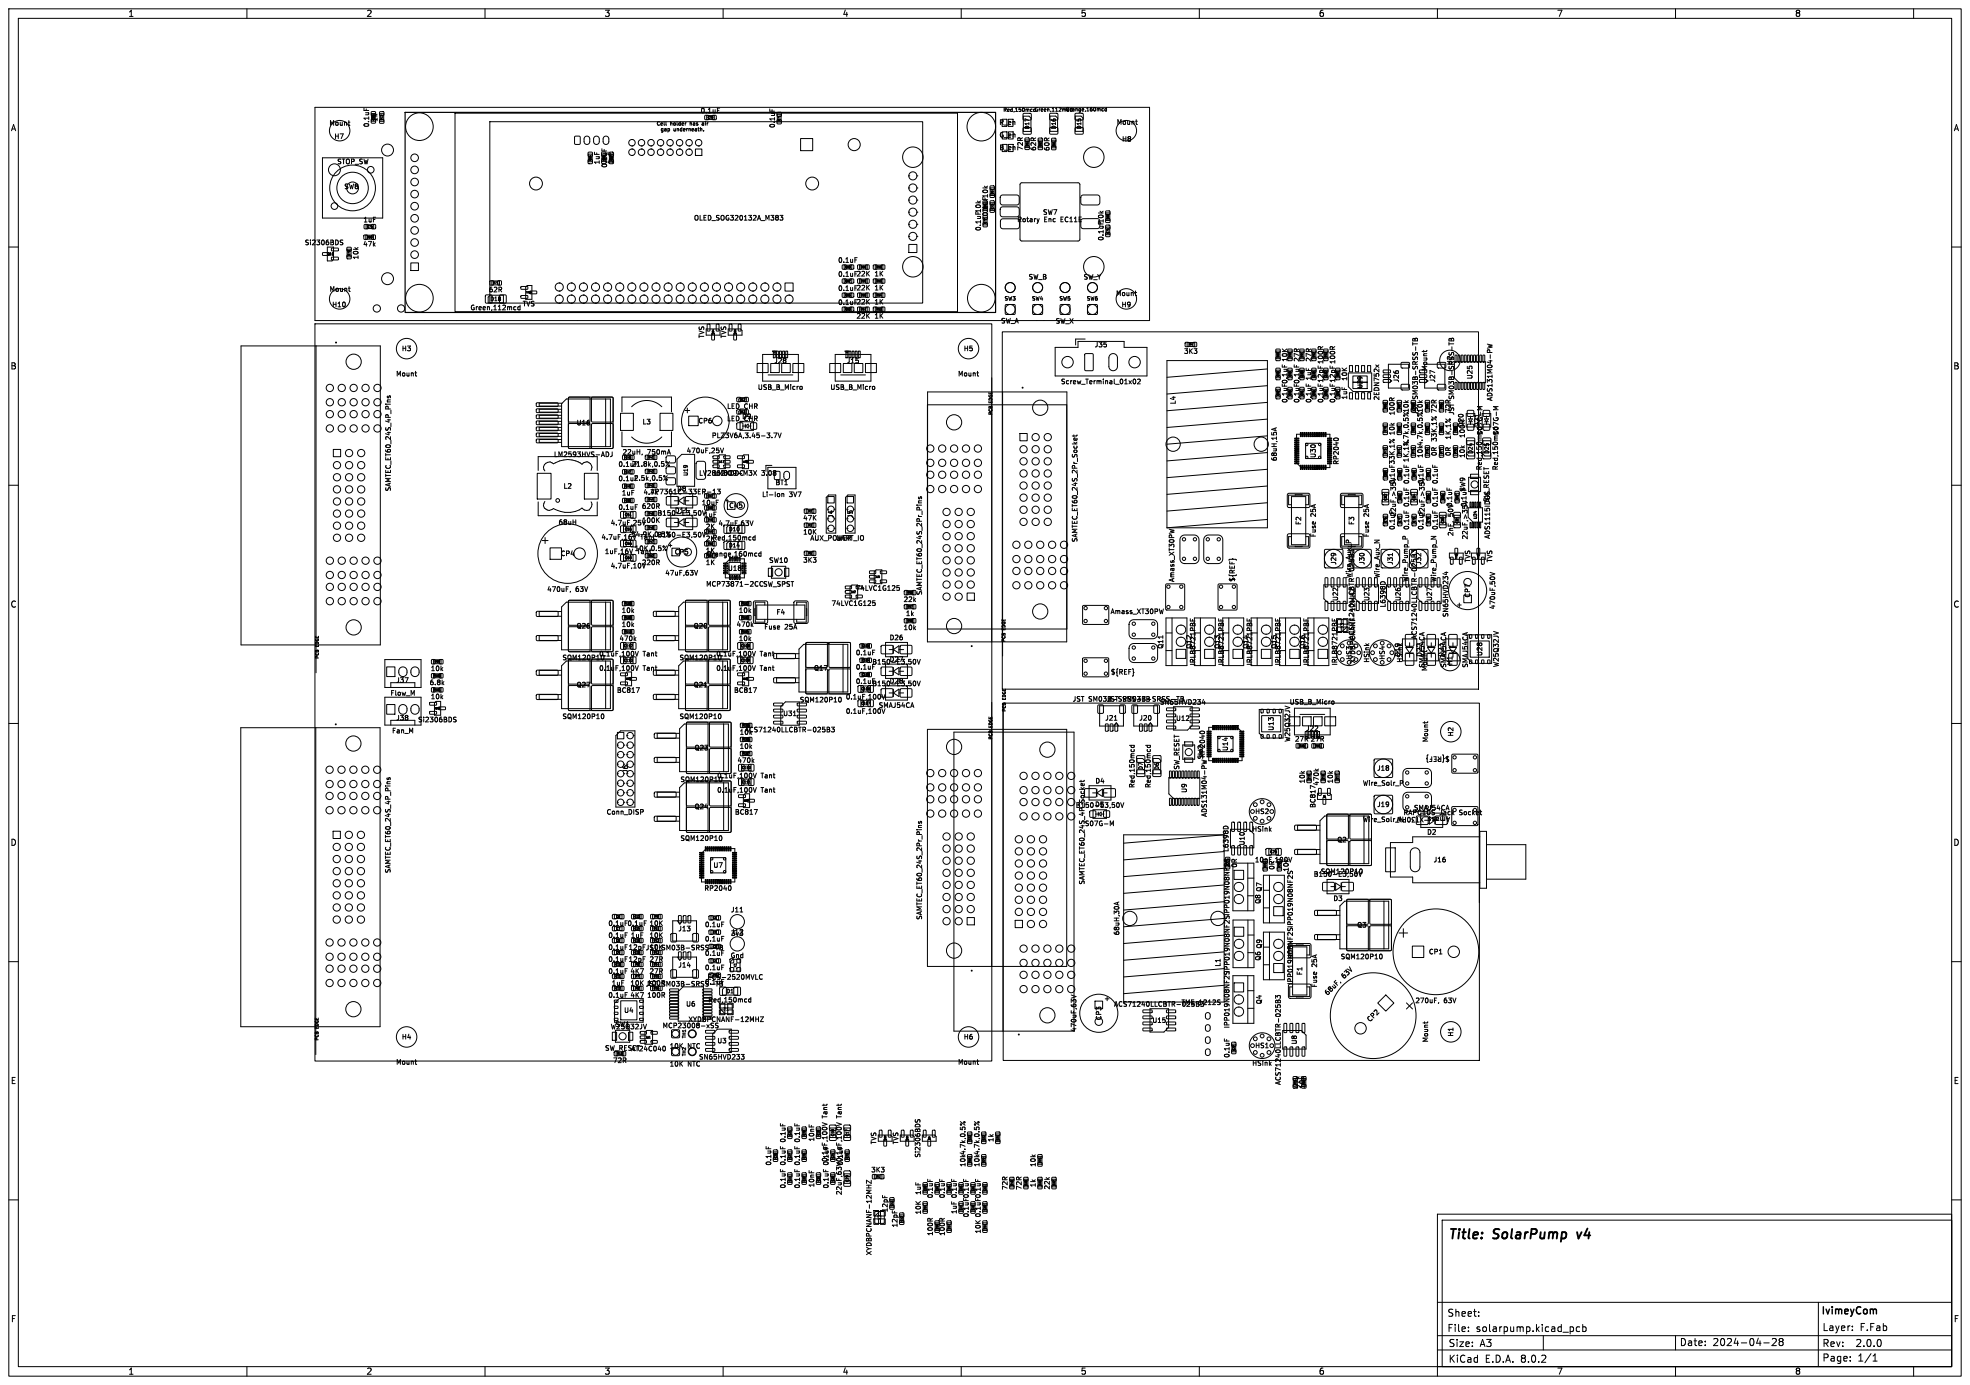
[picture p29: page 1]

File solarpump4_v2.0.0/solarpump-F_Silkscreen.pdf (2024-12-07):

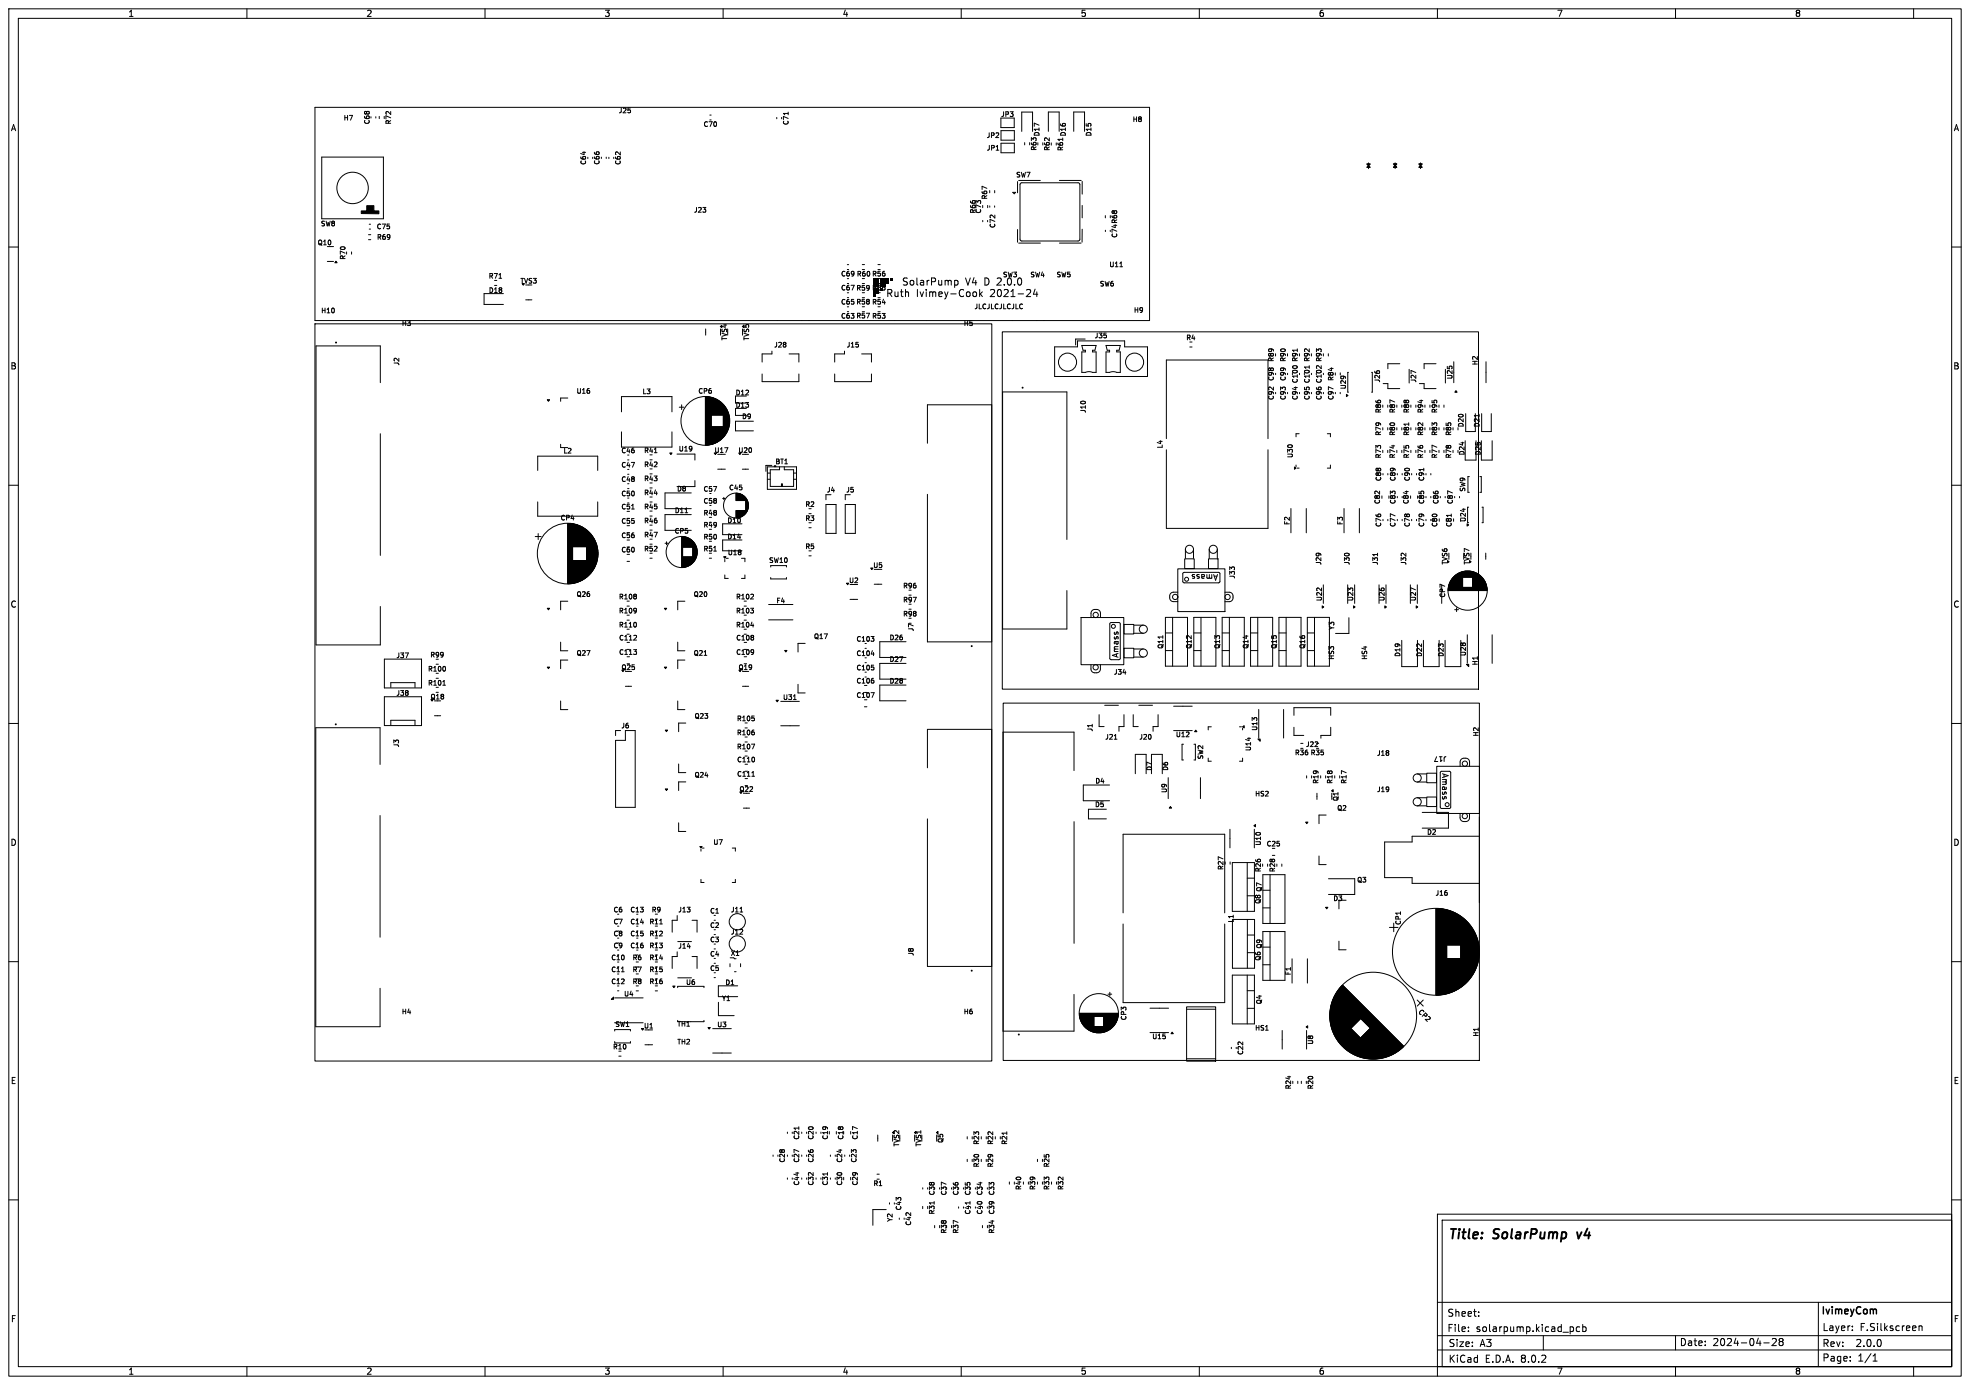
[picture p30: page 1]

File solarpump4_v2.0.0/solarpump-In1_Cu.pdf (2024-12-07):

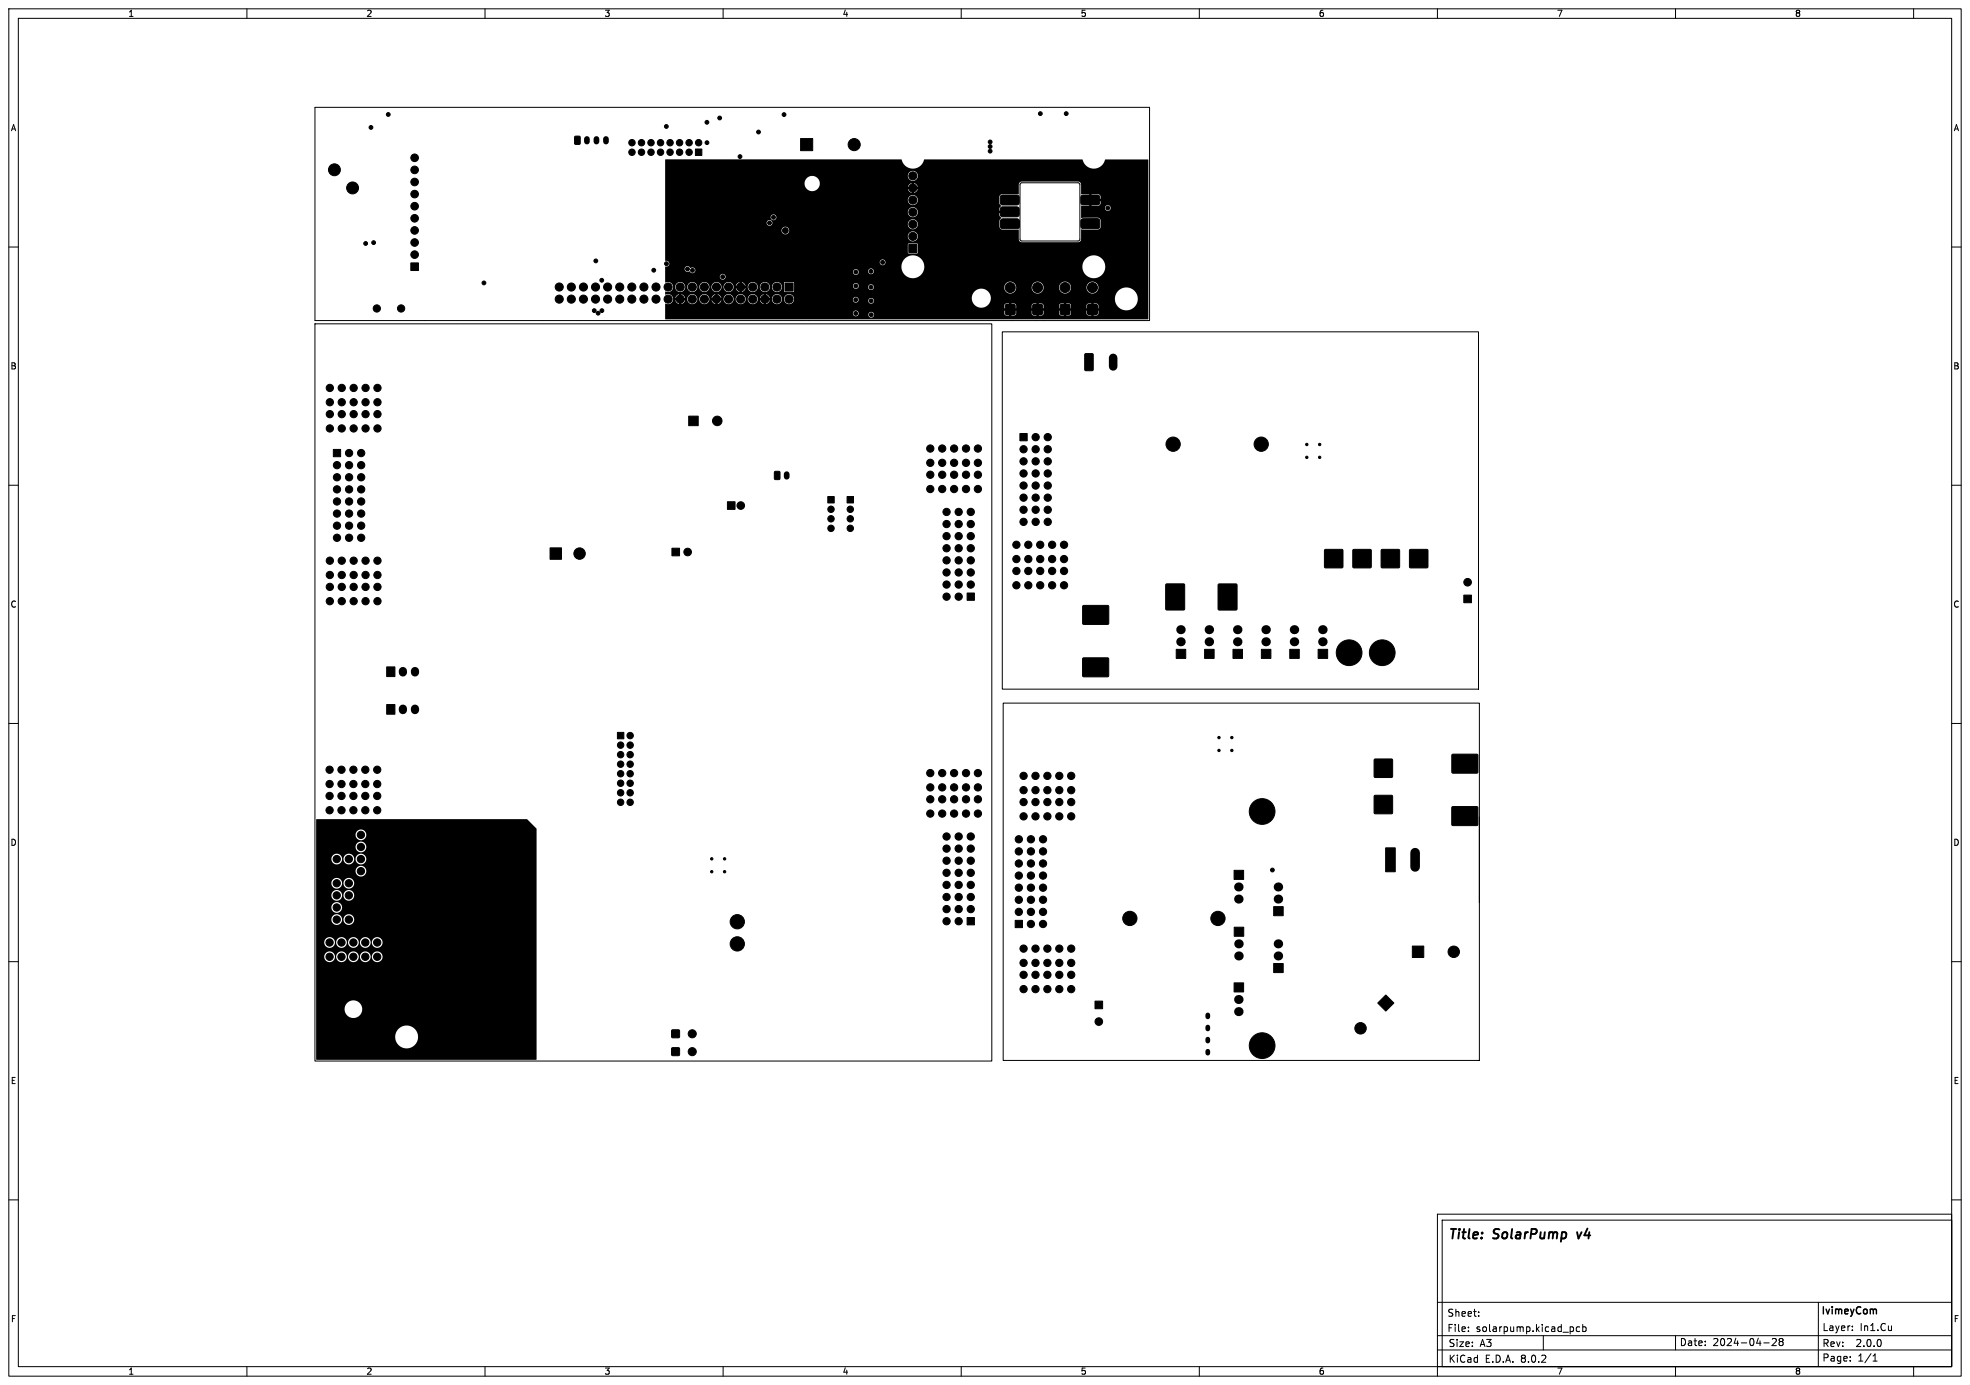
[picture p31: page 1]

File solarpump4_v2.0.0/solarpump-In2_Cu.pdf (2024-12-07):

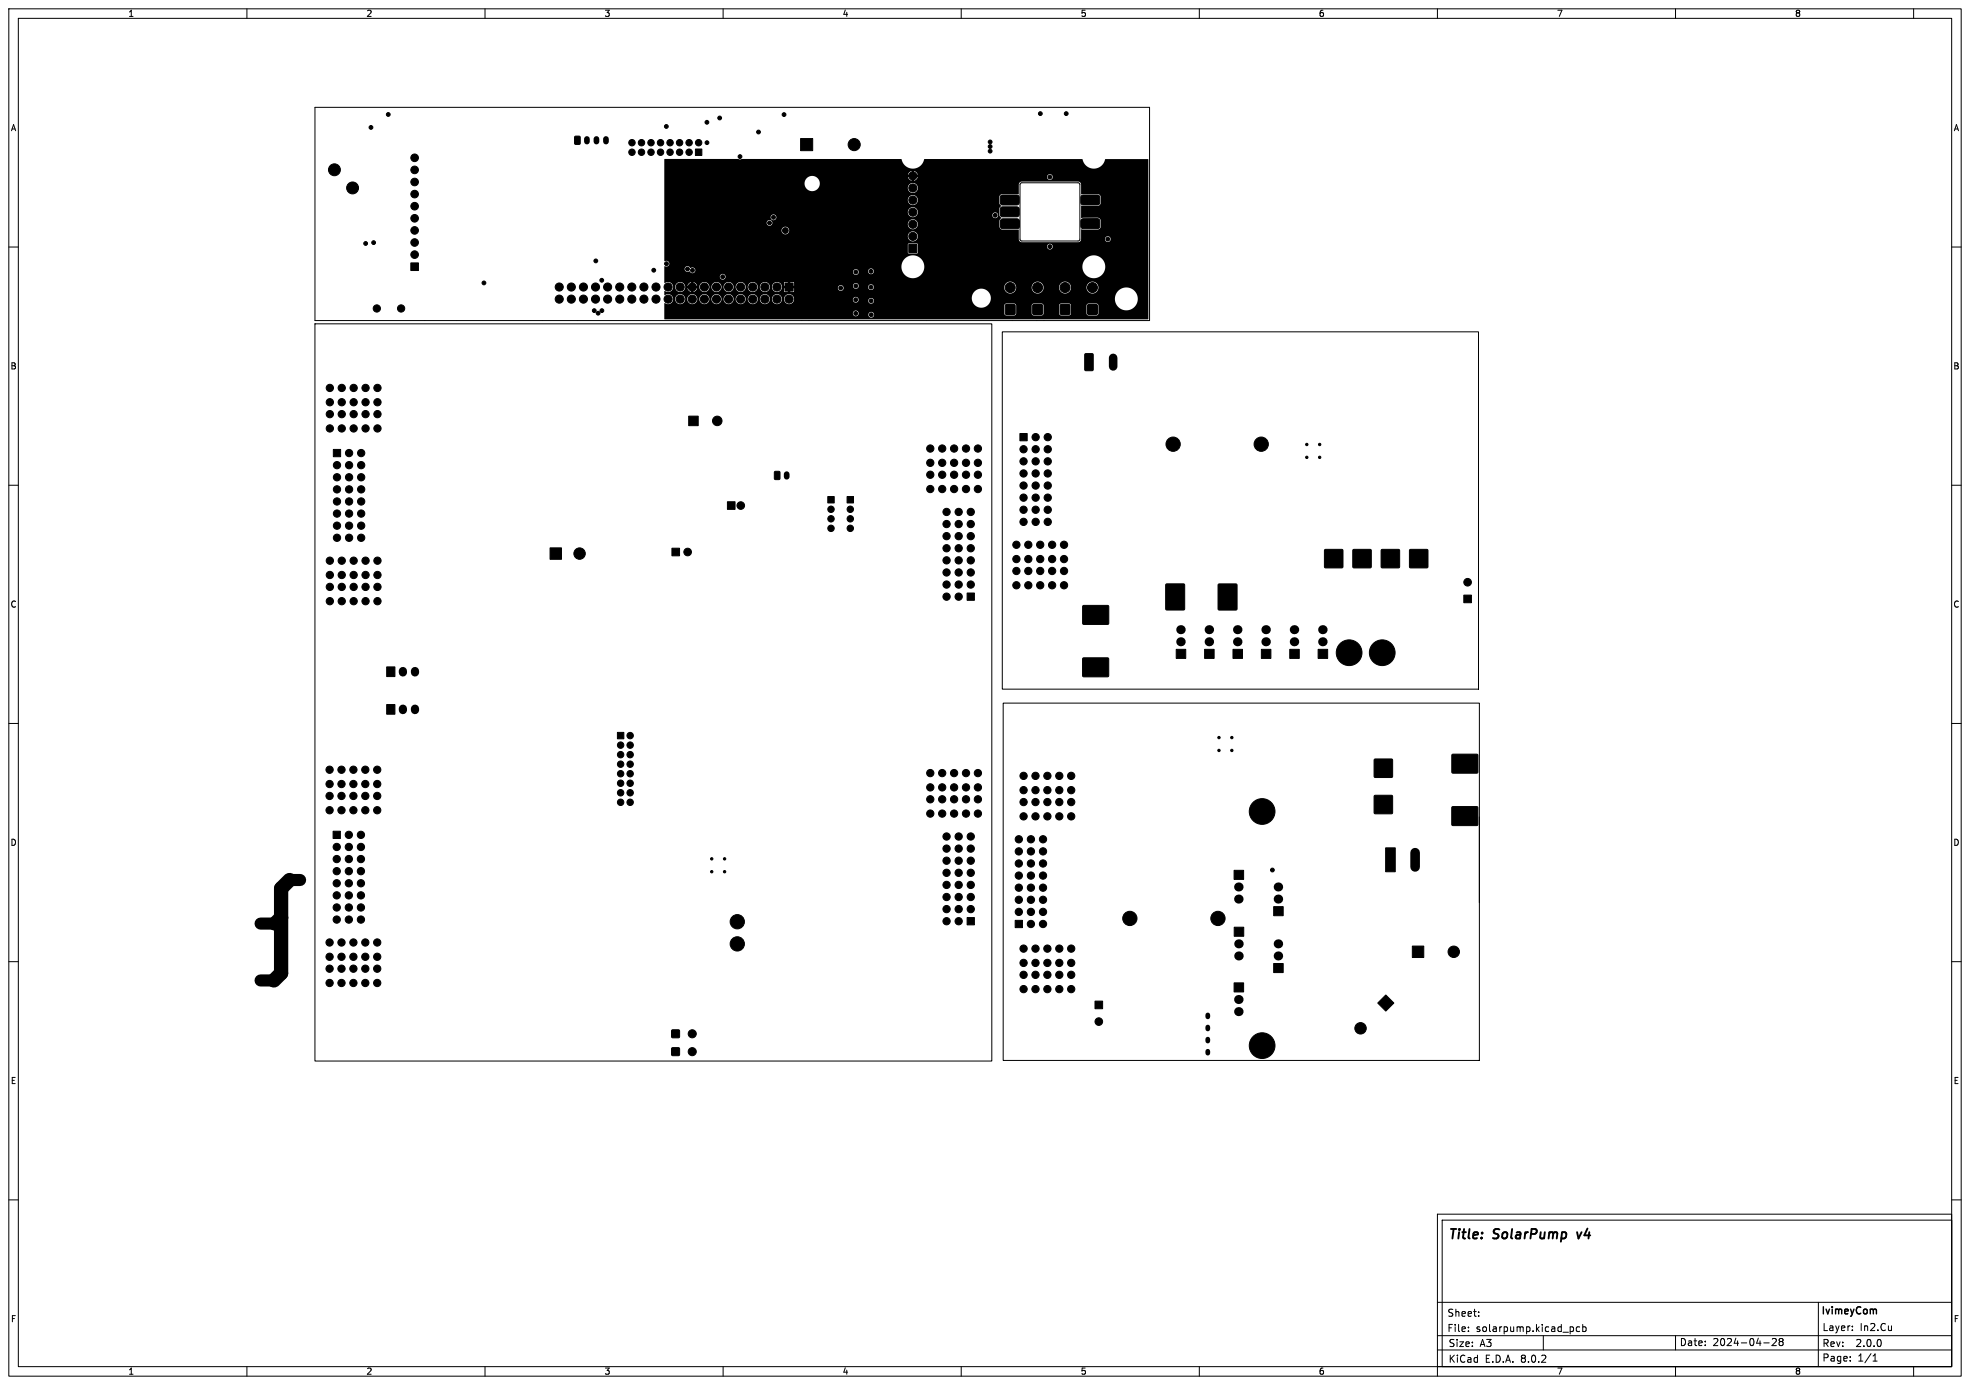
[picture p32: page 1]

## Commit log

2021-11-25 Update for v3
    [1050570001.step, 1241.1082.3.step, 387006308.step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]
2021-11-25 Additional pics, renders
    [solarpump.kicad_pcb, solarpump.kicad_sch]
2021-12-01 Update for Kicad 6-rc; replace 12V reg and cascade; add EEPROM;
    [battery.kicad_sch, frontpanel.kicad_sch, mcu.kicad_sch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]
2021-12-01 Update file perms;
    [Heatsink1.step, battery.kicad_sch, frontpanel.kicad_sch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]
2021-12-01 Fix diode FP errors, add models; link in regulator error sig; add new coil 3d model; lots of small tweaks
    [Coilcraft-MSS1278H.STEP, DO-214AC.STEP, DO-219AB.step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]
2021-12-03 Various important tweaks and fixes.
    Fix several incorrect capacitor footprints;
    Fix slightly incorrect footprint for USB connector;
    Add ground vias around MPPT circuit;
    Add Zener protection circuit for regulation error input;
    Use pin header not socket for Pico Display header;
    Fix missing connection to featherwing i2c;
    Add in 3d models for USB socket and switch
    Update kicad sheet dates;
    [1241.1082.8.STEP, USB1040-GF-L-B.step, battery.kicad_sch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]
2021-12-04 Adjust footprint silkscreen; modify EC11 FP to inset into board, and adjust display board
    [frontpanel.kicad_sch, solarpump.kicad_sch]
2021-12-05 Updat Step models via cad-assistant, refresh pdfs
    [1050570001.step, 1241.step, RP2040_Stamp.step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]
2021-12-11 Rework with larger display; update component selection; add SWD conn; add RTC chip and QWIIC i2c socket
    [battery.kicad_sch, frontpanel.kicad_sch, mcu.kicad_sch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]
2021-12-11 Some 3d models of the board; 3d models of 20x2 pin headers; commit more docs
    [REF-182683-02.step, REF-182684-02.step]
2021-12-12 Update footprint file modes
2021-12-12 Add step render of board; add circuit versions
2021-12-12 Use consistent property names for footprints
2021-12-13 More updates to regularise property names
    [battery.kicad_sch, frontpanel.kicad_sch, mcu.kicad_sch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]
2022-04-11 Fix some errors in the design (esp net-tie in wrong place)
    - correct led, diode footprints & model
    - fix fuse holder (bad hole spec)
    - update oled mod
    - update EC11 mod
    - add Blender models of case (xz compressed)
    - more updated gerbers (not current!)
    - improve layout of front panel pcb
    - delete unused files
    [DO-219AB.stp, Led RGB 5mm.STEP, OLED_SOG320132A_M383.step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]
2022-07-15 Adjust to supply 2 CS sigs to display; rename MISO to DC; larger conn cable.
    [battery.kicad_sch, frontpanel.kicad_sch, mcu.kicad_sch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]
2022-07-15 Toroid footprint
2022-07-15 Fixup file perms
    [battery.kicad_sch, frontpanel.kicad_sch, mcu.kicad_sch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]
2022-07-15 Lots of small changes; widen disp board to same as pwr board; use attiny mcu for rot-enc ctrl; switch to one board with cutline
    [frontpanel.kicad_sch, mcu.kicad_sch, mppt.kicad_sch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]
2024-03-13 Updated 3d models
    [1050570001.step, 1241.1082.3.step, 3-d-nc3faah2.step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]
2024-03-13 Schematic + pcb 1.3.3
    [battery.kicad_sch, frontpanel.kicad_sch, mcu.kicad_sch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]
2024-03-13 Intermediate versions, adjust file modes
    [battery.kicad_sch, frontpanel.kicad_sch, mcu.kicad_sch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]
2024-12-07 Connector and CAN models
    [AMASS-XT30PW-M.STEP, ET60S-000-3-08-D02-L-R1-S.step, ET60S-D02-3-08-D02-L-R1-S.stp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]
2024-12-07 Connector footprints
2024-12-07 Datasheets for ET connectors
2024-12-07 Further works...
    [flow_fan.kicad_sch, battery.kicad_sch, flow_fan.kicad_sch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]
2025-03-25 pcb net updates
    [solarpump.kicad_pcb]

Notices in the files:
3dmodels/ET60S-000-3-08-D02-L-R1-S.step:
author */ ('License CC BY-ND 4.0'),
